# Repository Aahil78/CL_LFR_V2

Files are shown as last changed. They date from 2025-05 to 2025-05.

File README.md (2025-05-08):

# Cyber Link's LFR V2

This bot is Cyber Link's Line Follower V2 (Originally named L2-B2)

# Features
- The PCB is the chassis
- It's compact
- It uses the ESP32-S3, QTR-8RC, TB6612FNG, IP2721 PD Sink IC, etc.
- It has holes to mount two N20 Micro gear motors
- It is high speed and has pads to add 3x Li-ion batteries or holders.
- And more!

# More to come soon!

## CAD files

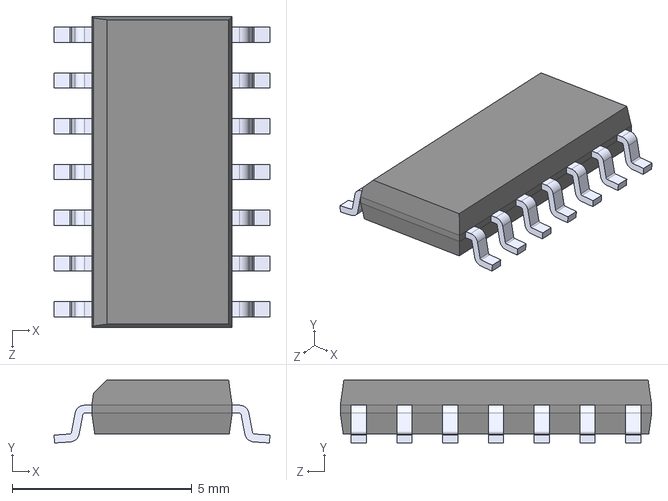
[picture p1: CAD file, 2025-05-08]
parts/74HC125/74HC125.step
6.00 x 1.75 x 8.65 mm

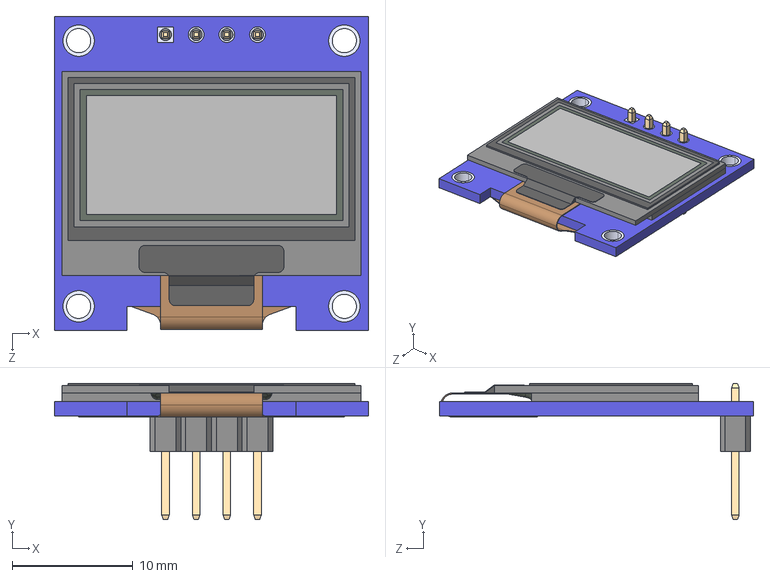
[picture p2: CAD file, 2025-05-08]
parts/DM-OLED096-636/DM-OLED096-636.step
26.0 x 11.3 x 26.0 mm
DM-OLED096-636_Module
DM-OLED096-636_Panel

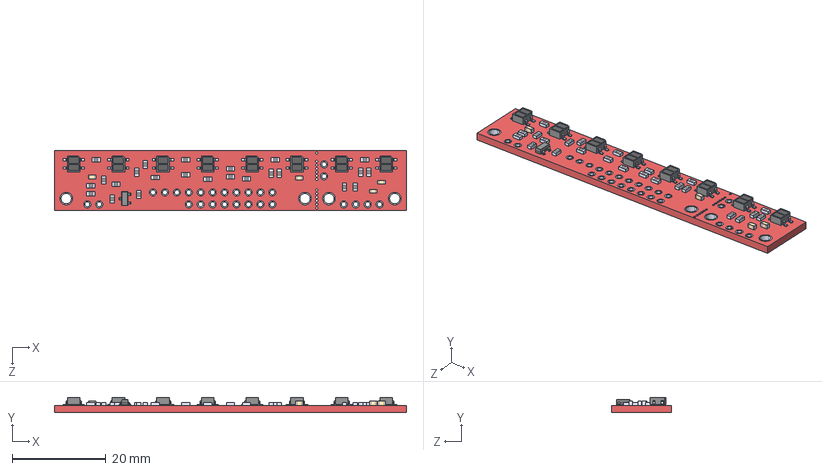
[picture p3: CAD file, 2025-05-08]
parts/QTR-8X/QTR-8A.step
74.9 x 3.27 x 12.7 mm
QTR-8A_QTR-8A
QRE1113GR_QRE1113GR x 8

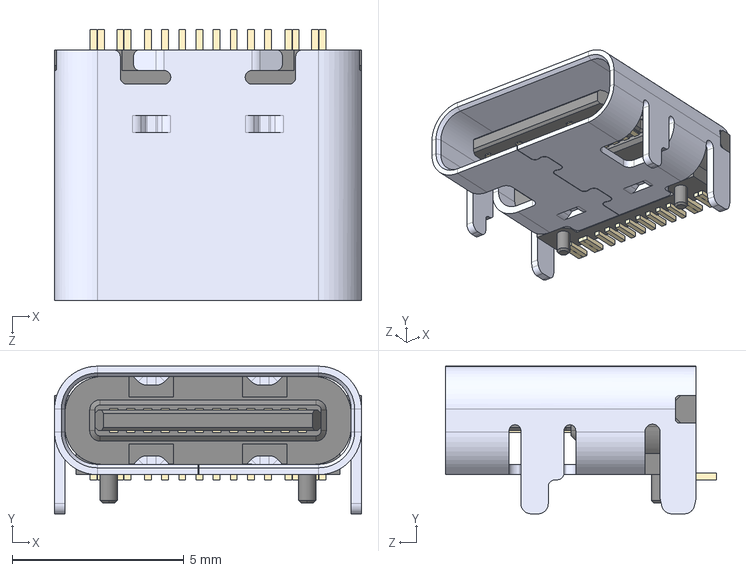
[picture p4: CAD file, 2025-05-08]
parts/TYPE-C-31-M-12/TYPE-C-31-M-12.step
8.94 x 4.30 x 7.90 mm

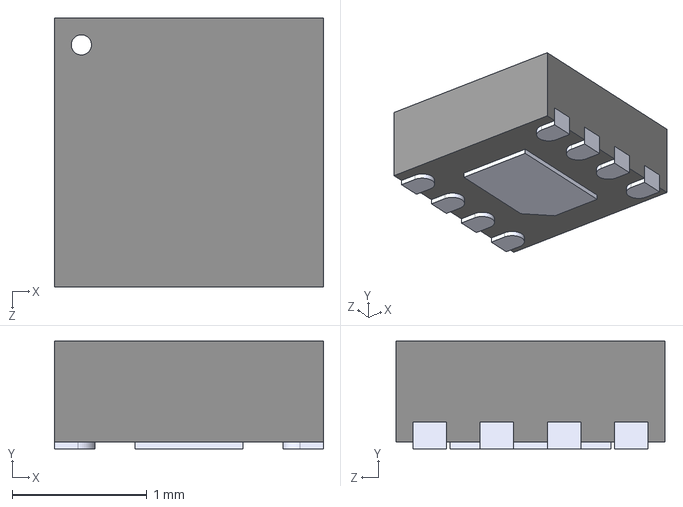
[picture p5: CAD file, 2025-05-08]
parts/MAX17048G_T10/MAX17048G_T10.step
2.00 x 0.8 x 2.00 mm

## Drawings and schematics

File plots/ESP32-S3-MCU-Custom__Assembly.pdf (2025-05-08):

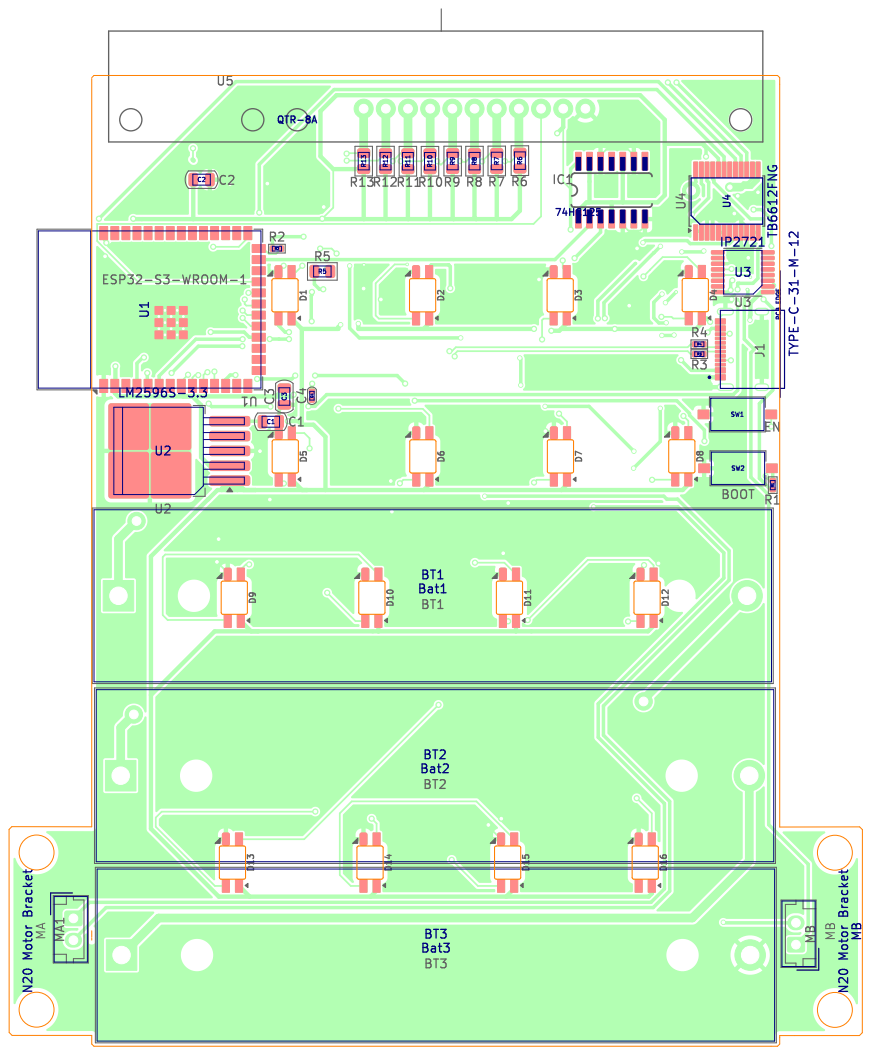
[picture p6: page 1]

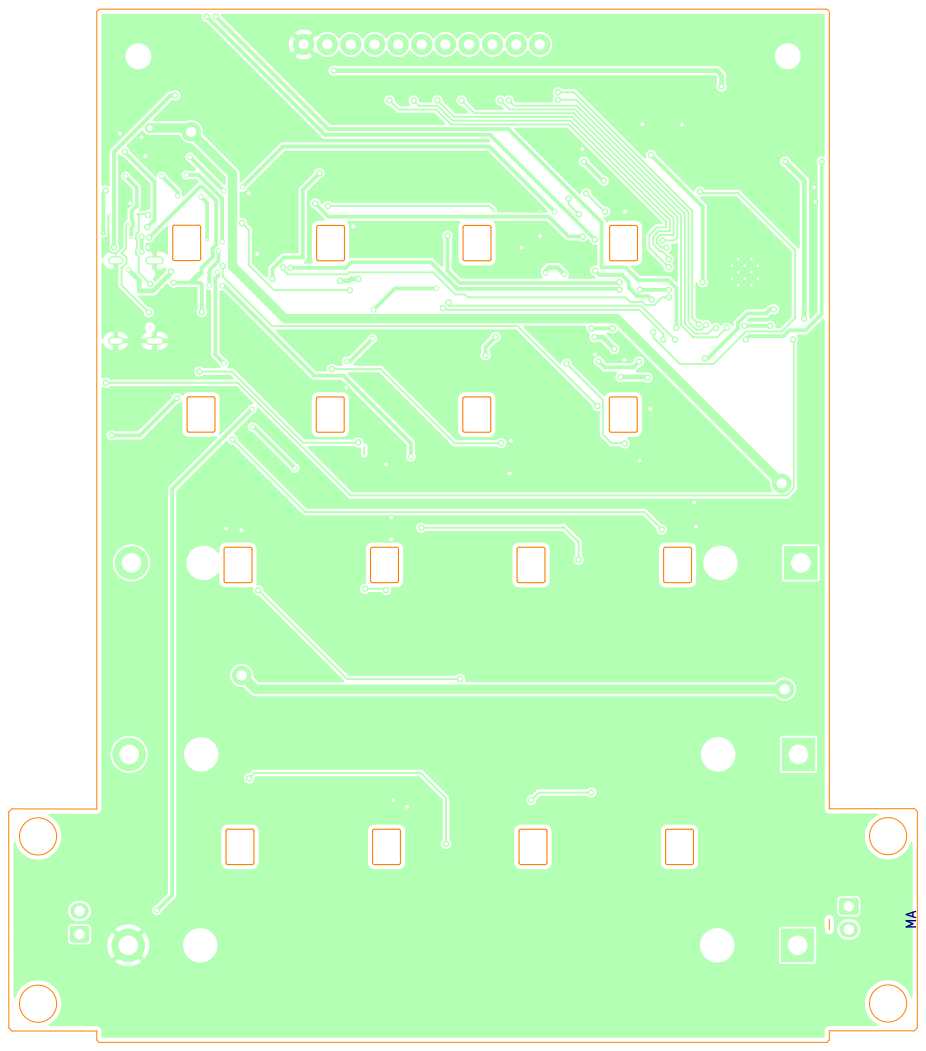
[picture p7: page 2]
D Date: KiCad; E.D.A. 9.0.1 Size: A4; Rev:; Id: /1 Title: File: ESP32-S3-MCU-Custom.kicad_pcb Sheet: Colored; BOT Board2Pdf:; Colored; BOT -; Page 2/2

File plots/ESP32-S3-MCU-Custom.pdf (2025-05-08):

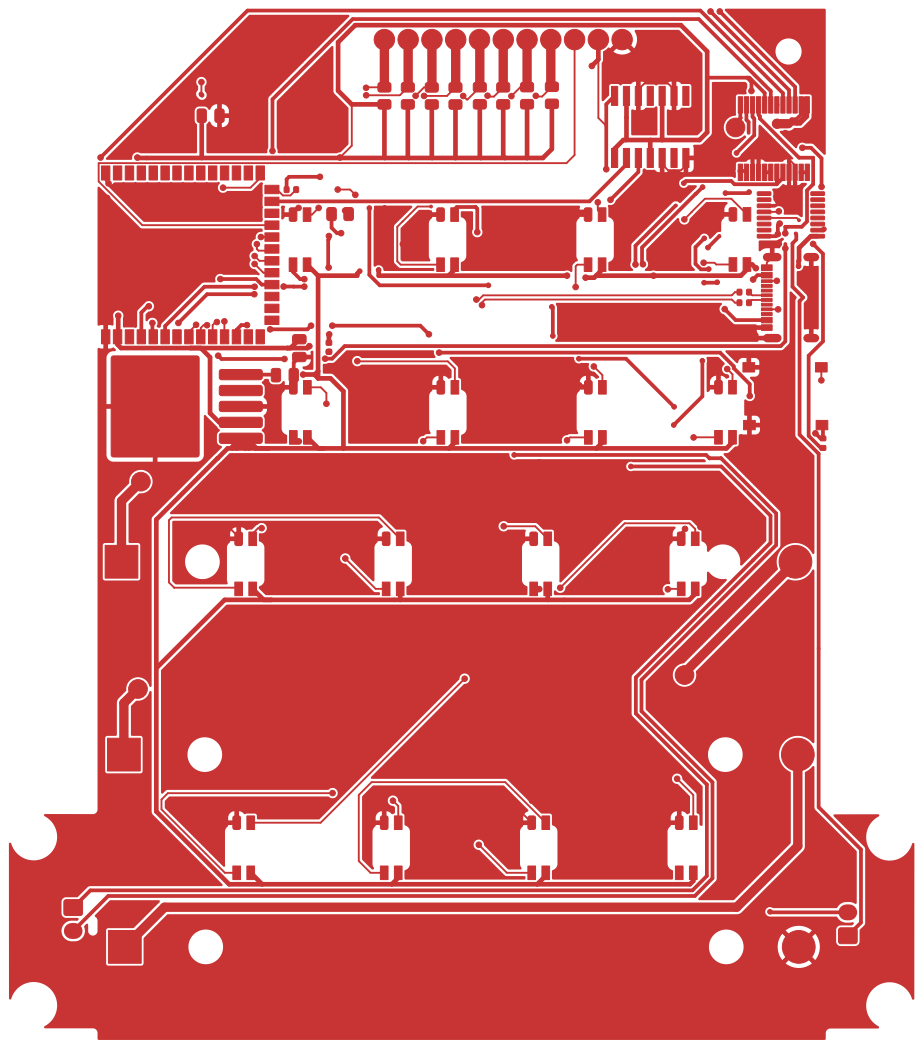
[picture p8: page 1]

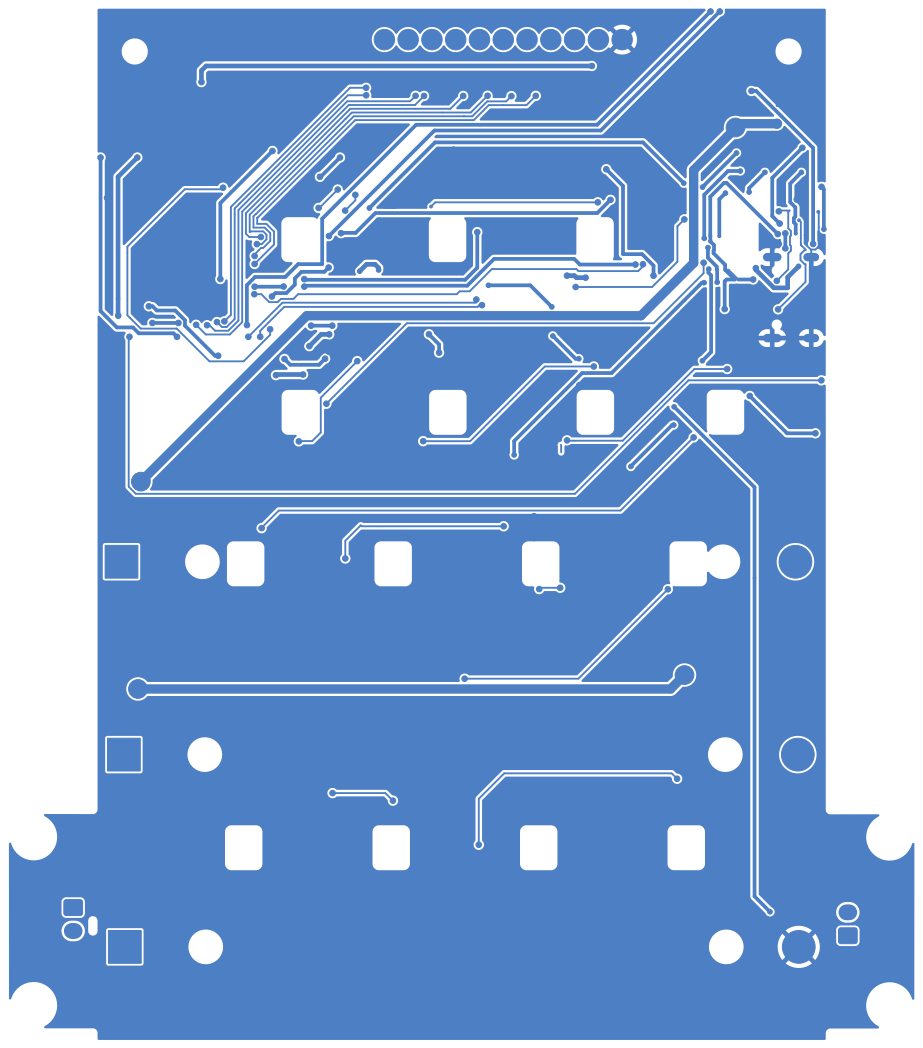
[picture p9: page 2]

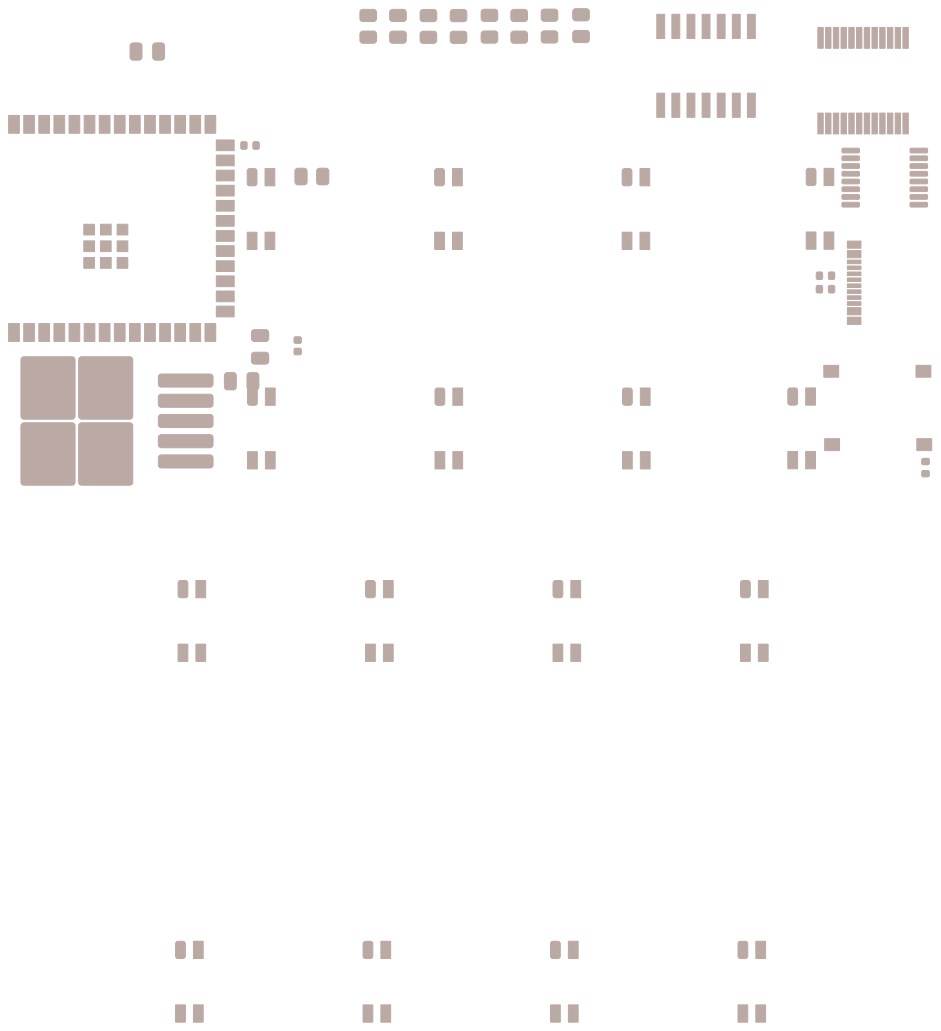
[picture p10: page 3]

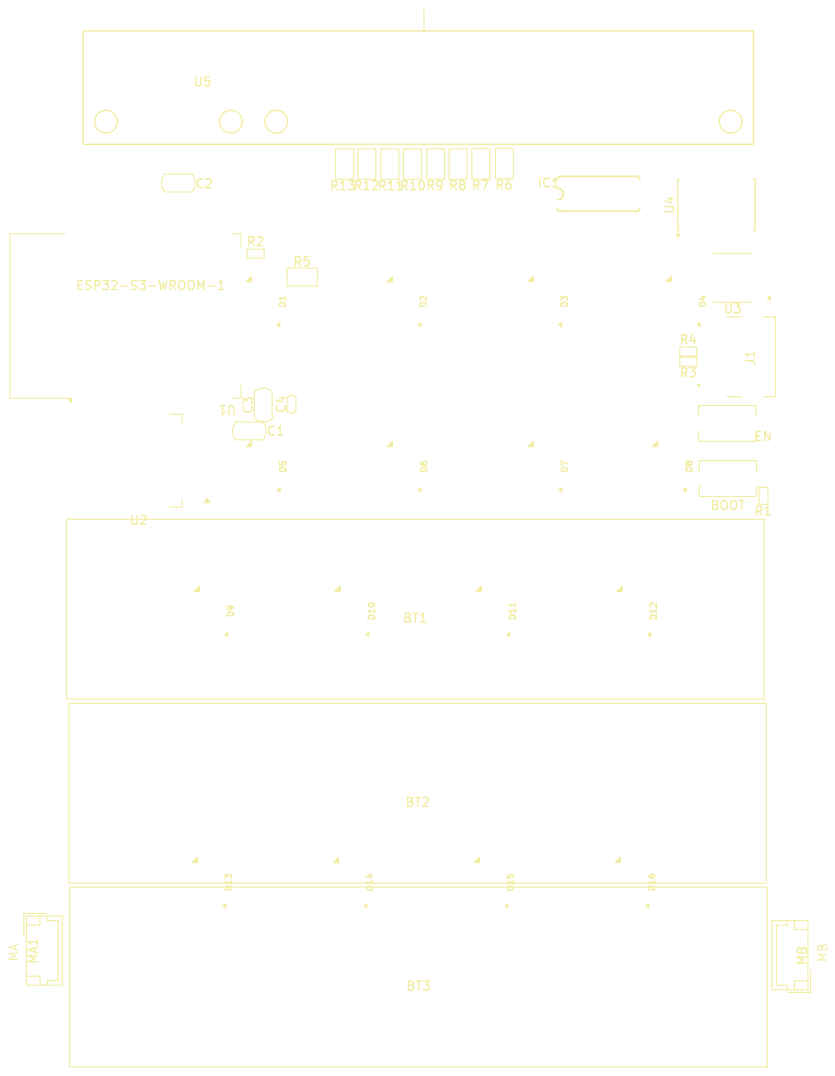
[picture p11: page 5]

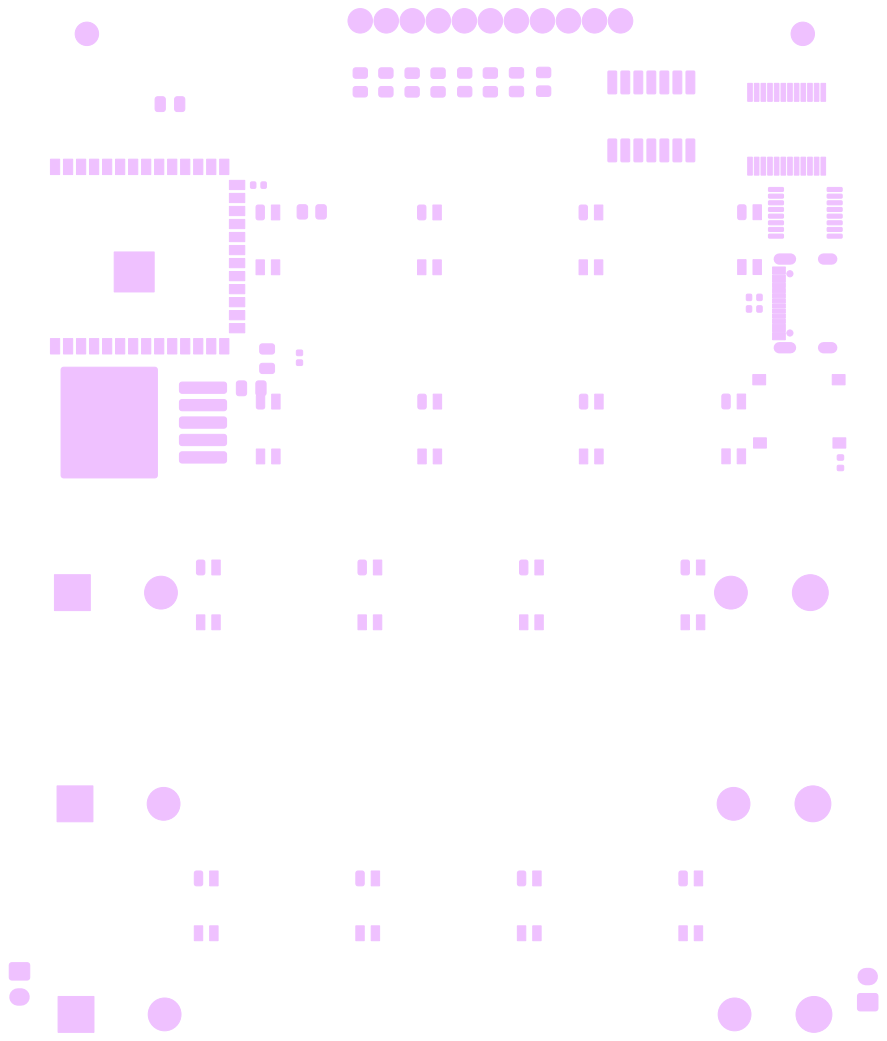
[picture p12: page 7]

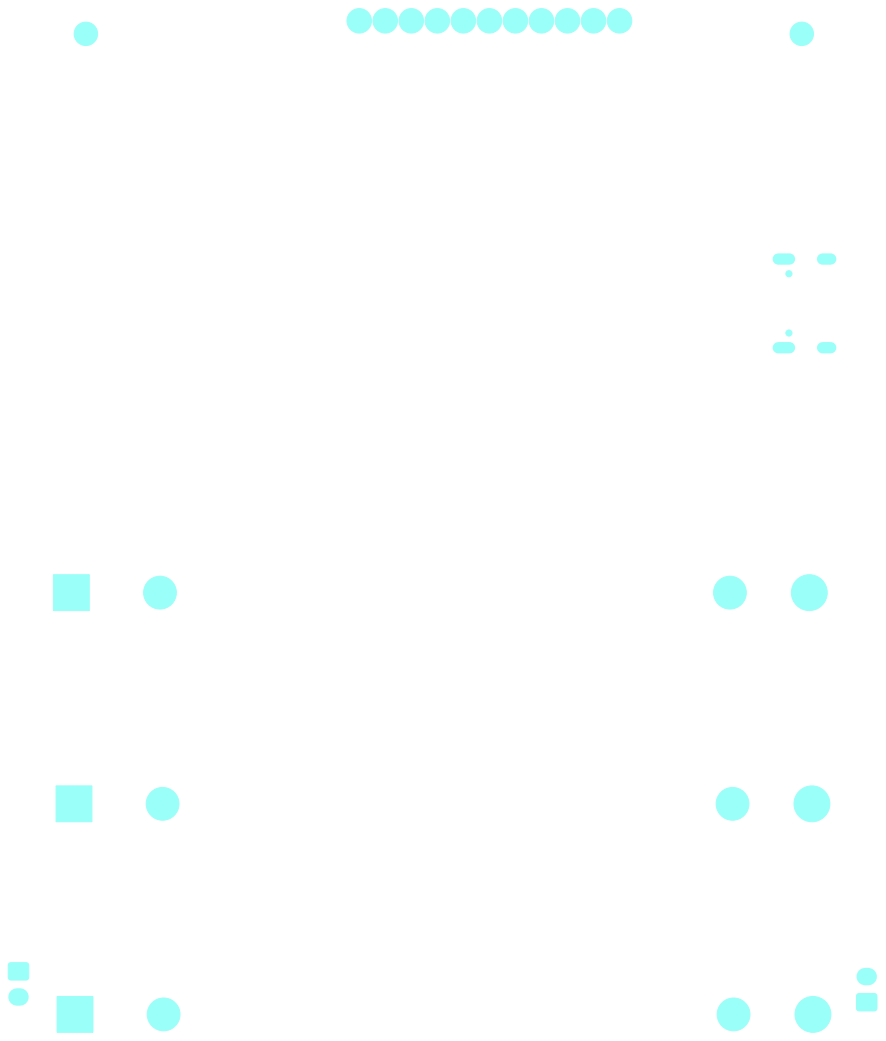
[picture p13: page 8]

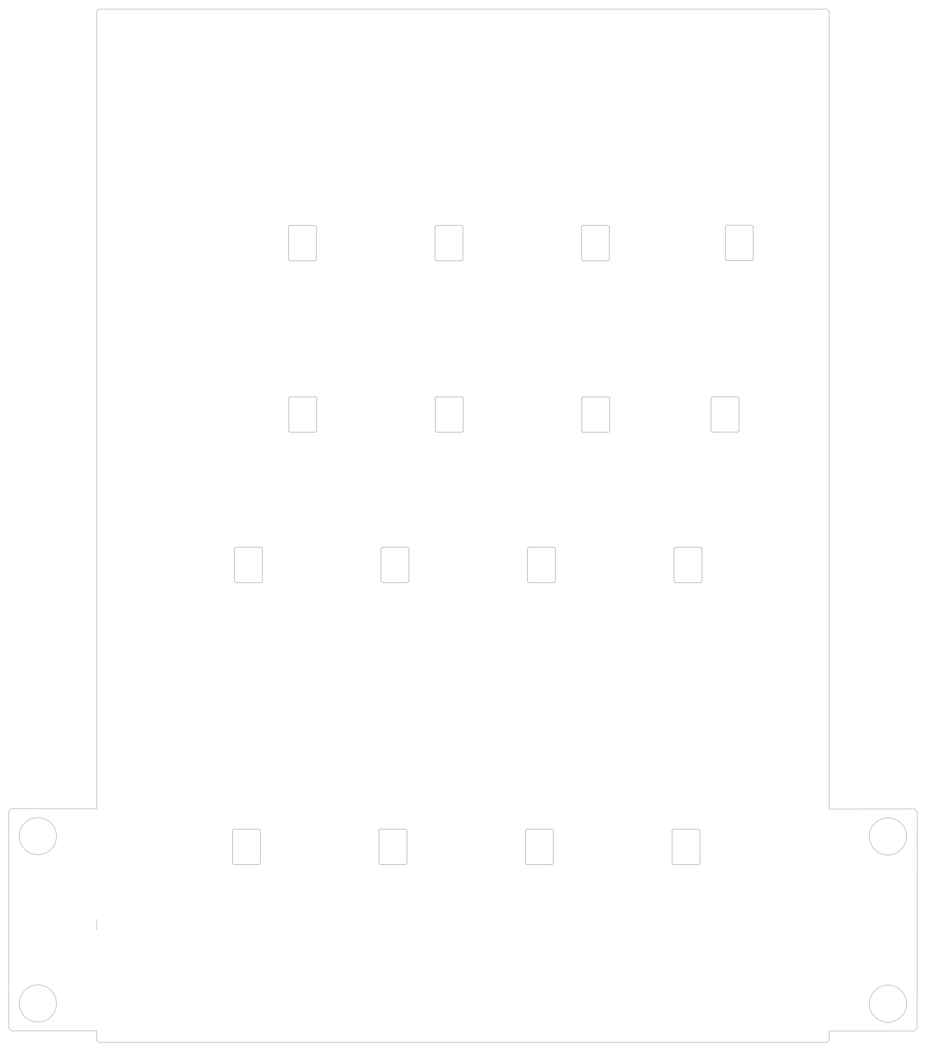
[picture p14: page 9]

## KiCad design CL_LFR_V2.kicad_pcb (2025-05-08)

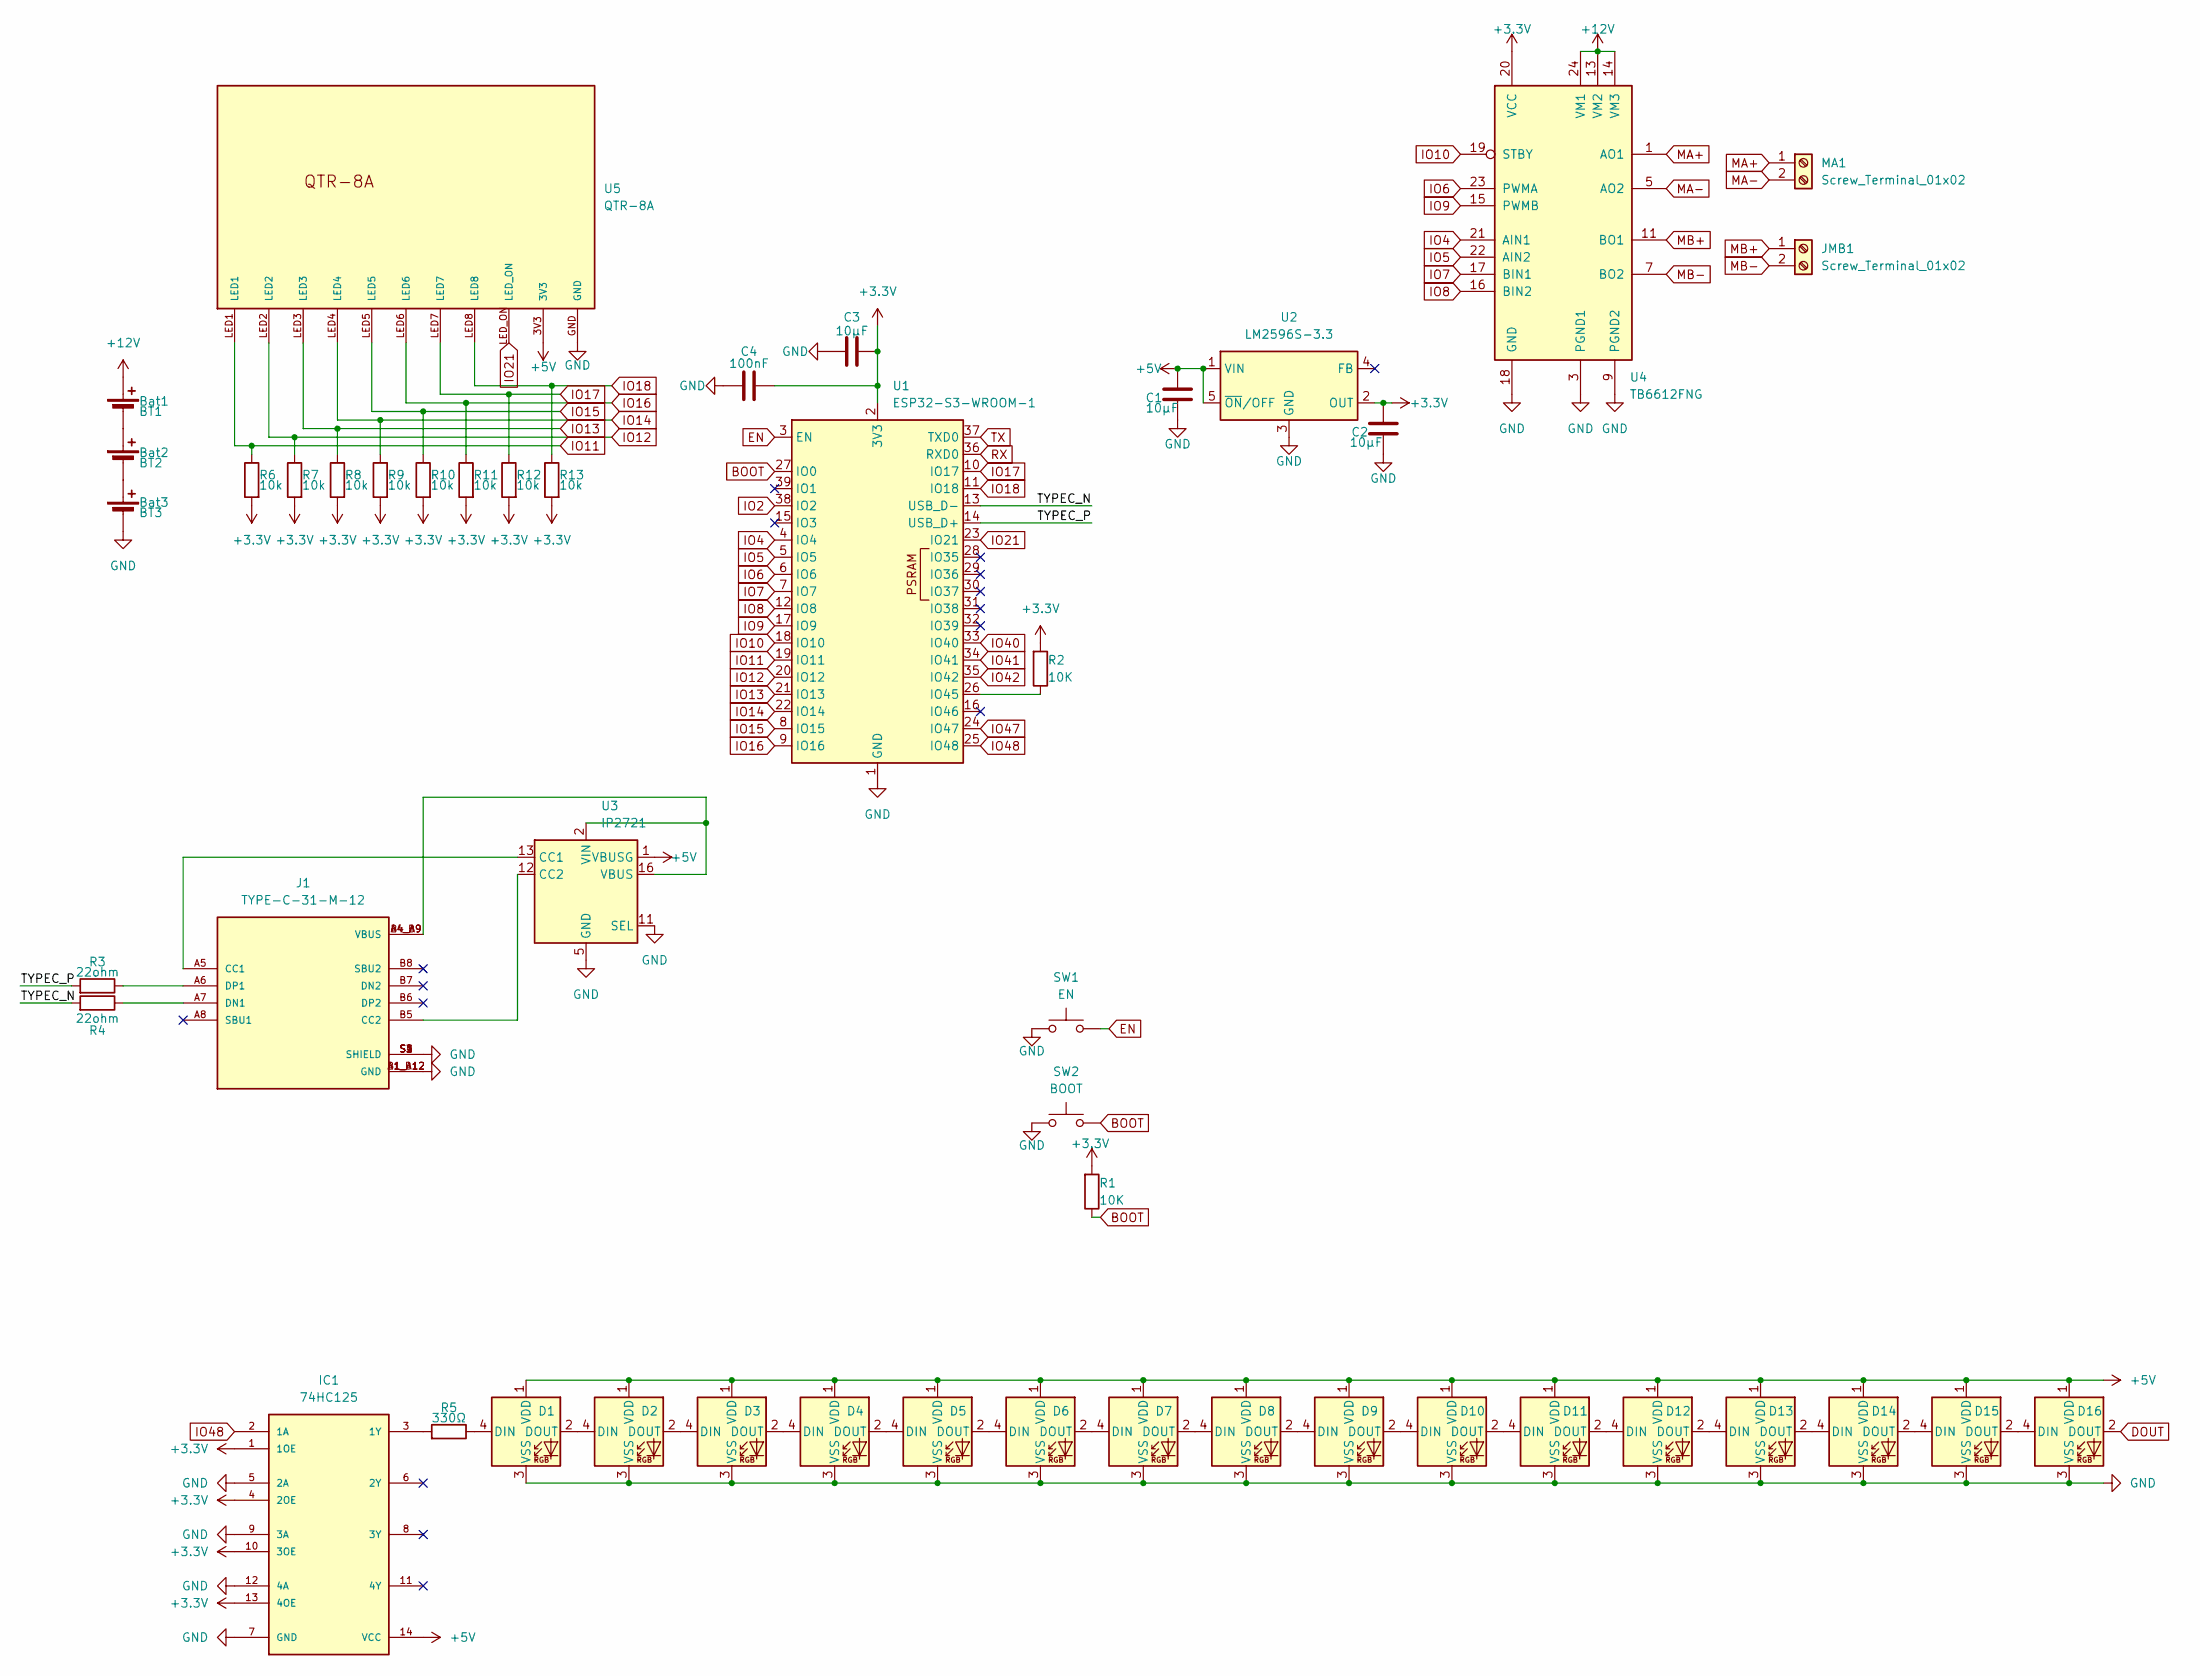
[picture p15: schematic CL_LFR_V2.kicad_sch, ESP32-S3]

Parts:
BT1: Bat1; BatteryHolder_MPD_BH-18650-PC2
BT2: Bat2; BatteryHolder_MPD_BH-18650-PC2
BT3: Bat3; BatteryHolder_MPD_BH-18650-PC2
C1, C2, C3: 10µF; C_0805_2012Metric
C4: 100nF; C_0402_1005Metric
D1, D2, D3, D4, D5, D6, D7, D8, D9, D10, D11, D12, D13, D14, D15, D16: SK6812MINI; SK6812-MINI-E
IC1: 74HC125; SOIC-14
J1: TYPE-C-31-M-12; HRO_TYPE-C-31-M-12; PARTREV 2020.12.08
JMB1: Screw_Terminal_01x02; JST_EH_B2B-EH-A_1x02_P2.50mm_Vertical
MA1: Screw_Terminal_01x02; JST_EH_B2B-EH-A_1x02_P2.50mm_Vertical
R1, R2: 10K; R_0402_1005Metric
R3, R4: 22ohm; R_0402_1005Metric
R5: 330Ω; R_0805_2012Metric
R6, R7, R8, R9, R10, R11, R12, R13: 10k; R_0805_2012Metric
SW1: EN; SW_Tactile_SPST_NO_Straight_CK_PTS636Sx25SMTRLFS
SW2: BOOT; SW_Tactile_SPST_NO_Straight_CK_PTS636Sx25SMTRLFS
U1: ESP32-S3-WROOM-1
U2: LM2596S-3.3; TO-263-5_TabPin3
U3: IP2721; TSSOP-16_4.4x5mm_P0.65mm
U4: TB6612FNG; SSOP-24_5.3x8.2mm_P0.65mm
U5: QTR-8A

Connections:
+3.3V: C2.1, C3.2, C4.2, IC1.1 (1OE), IC1.4 (2OE), IC1.10 (3OE), IC1.13 (4OE), R1.1, R2.1, R6.1, R7.1, R8.1, R9.1, R10.1, R11.1, R12.1, R13.1, U1.2 (3V3), U2.2 (OUT), U4.20 (VCC)
+5V: C1.1, D1.1 (VDD), D2.1 (VDD), D3.1 (VDD), D4.1 (VDD), D5.1 (VDD), D6.1 (VDD), D7.1 (VDD), D8.1 (VDD), D9.1 (VDD), D10.1 (VDD), D11.1 (VDD), D12.1 (VDD), D13.1 (VDD), D14.1 (VDD), D15.1 (VDD), D16.1 (VDD), IC1.14 (VCC), U2.1 (VIN), U2.5 (~ON/OFF), U3.1 (VBUSG), U5.3V3
+12V: BT1.1 (+), U4.13 (VM2), U4.14 (VM3), U4.24 (VM1)
/TYPEC_N: R4.1, U1.13 (USB_D-)
/TYPEC_P: R3.1, U1.14 (USB_D+)
BOOT: R1.2, SW2.2, U1.27 (IO0)
DOUT: D16.2 (DOUT)
EN: SW1.2, U1.3 (EN)
GND: BT3.2 (-), C1.2, C2.2, C3.1, C4.1, D1.3 (VSS), D2.3 (VSS), D3.3 (VSS), D4.3 (VSS), D5.3 (VSS), D6.3 (VSS), D7.3 (VSS), D8.3 (VSS), D9.3 (VSS), D10.3 (VSS), D11.3 (VSS), D12.3 (VSS), D13.3 (VSS), D14.3 (VSS), D15.3 (VSS), D16.3 (VSS), IC1.5 (2A), IC1.7 (GND), IC1.9 (3A), IC1.12 (4A), J1.A1_B12 (GND), J1.B1_A12 (GND), J1.S1 (SHIELD), J1.S2 (SHIELD), J1.S3 (SHIELD), J1.S4 (SHIELD), SW1.1, SW2.1, U1.1 (GND), U1.40 (GND), U1.41 (GND), U2.3 (GND), U3.5 (GND), U3.11 (SEL), U4.3 (PGND1), U4.4 (PGND1), U4.9 (PGND2), U4.10 (PGND2), U4.18 (GND), U5.GND
IO2: U1.38 (IO2)
IO4: U1.4 (IO4), U4.21 (AIN1)
IO5: U1.5 (IO5), U4.22 (AIN2)
IO6: U1.6 (IO6), U4.23 (PWMA)
IO7: U1.7 (IO7), U4.17 (BIN1)
IO8: U1.12 (IO8), U4.16 (BIN2)
IO9: U1.17 (IO9), U4.15 (PWMB)
IO10: U1.18 (IO10), U4.19 (STBY)
IO11: R6.2, U1.19 (IO11), U5.LED1
IO12: R7.2, U1.20 (IO12), U5.LED2
IO13: R8.2, U1.21 (IO13), U5.LED3
IO14: R9.2, U1.22 (IO14), U5.LED4
IO15: R10.2, U1.8 (IO15), U5.LED5
IO16: R11.2, U1.9 (IO16), U5.LED6
IO17: R12.2, U1.10 (IO17), U5.LED7
IO18: R13.2, U1.11 (IO18), U5.LED8
IO21: U1.23 (IO21), U5.LED_ON
IO40: U1.33 (IO40)
IO41: U1.34 (IO41)
IO42: U1.35 (IO42)
IO47: U1.24 (IO47)
IO48: IC1.2 (1A), U1.25 (IO48)
MA+: MA1.1, U4.1 (AO1), U4.2 (AO1)
MA-: MA1.2, U4.5 (AO2), U4.6 (AO2)
MB+: JMB1.1, U4.11 (BO1), U4.12 (BO1); also elsewhere on the board
MB-: JMB1.2, U4.7 (BO2), U4.8 (BO2); also elsewhere on the board
unnamed: BT1.2 (-), BT2.1 (+)
unnamed: BT2.2 (-), BT3.1 (+)
unnamed: D1.2 (DOUT), D2.4 (DIN)
unnamed: D2.2 (DOUT), D3.4 (DIN)
unnamed: D3.2 (DOUT), D4.4 (DIN)
unnamed: D4.2 (DOUT), D5.4 (DIN)
unnamed: D5.2 (DOUT), D6.4 (DIN)
unnamed: D6.2 (DOUT), D7.4 (DIN)
unnamed: D7.2 (DOUT), D8.4 (DIN)
unnamed: D8.2 (DOUT), D9.4 (DIN)
unnamed: D9.2 (DOUT), D10.4 (DIN)
unnamed: D10.2 (DOUT), D11.4 (DIN)
unnamed: D11.2 (DOUT), D12.4 (DIN)
unnamed: D12.2 (DOUT), D13.4 (DIN)
unnamed: D13.2 (DOUT), D14.4 (DIN)
unnamed: D14.2 (DOUT), D15.4 (DIN)
unnamed: D15.2 (DOUT), D16.4 (DIN)
unnamed: IC1.3 (1Y), R5.1
unnamed: J1.A5 (CC1), U3.13 (CC1)
unnamed: J1.B5 (CC2), U3.12 (CC2)
unnamed: J1.A7 (DN1), R4.2
unnamed: J1.A6 (DP1), R3.2
unnamed: R2.2, U1.26 (IO45)
unnamed: J1.A4_B9 (VBUS), J1.B4_A9 (VBUS), U3.2 (VIN), U3.16 (VBUS)
RX: U1.36 (RXD0)
TX: U1.37 (TXD0)

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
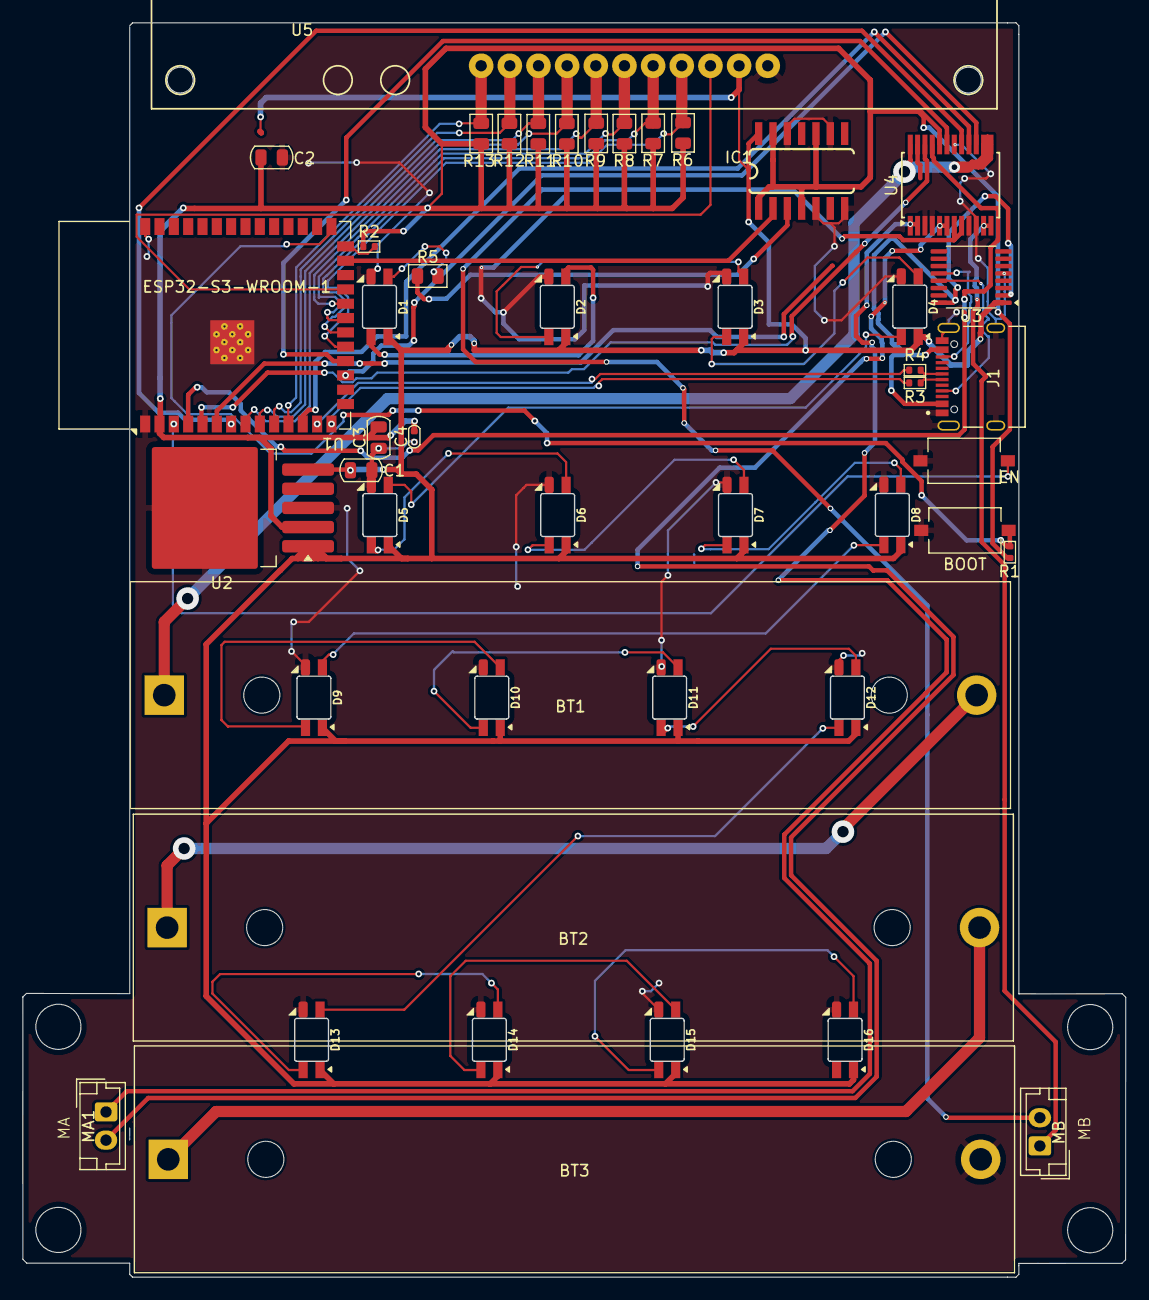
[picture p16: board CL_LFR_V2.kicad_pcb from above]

Board: 2 copper layers, 97.7 x 111.2 mm, 49 parts (1 on the bottom side), 53 nets.

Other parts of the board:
MA: N20 Motor Bracket; N20 Bracket
MB: Screw_Terminal_01x02; JST_EH_B2B-EH-A_1x02_P2.50mm_Vertical
MB#2: N20 Motor Bracket; N20 Bracket

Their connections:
MB+: MB.1; also elsewhere on the board
MB-: MB.2; also elsewhere on the board
